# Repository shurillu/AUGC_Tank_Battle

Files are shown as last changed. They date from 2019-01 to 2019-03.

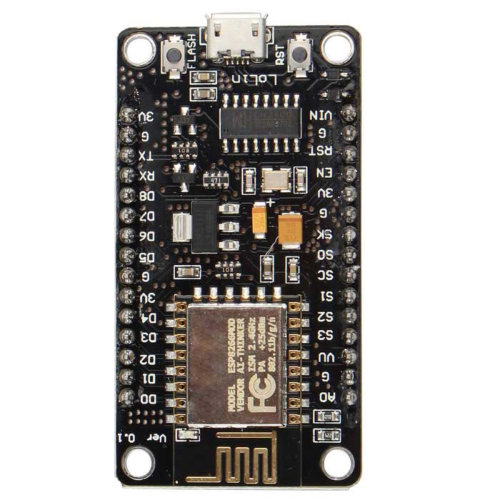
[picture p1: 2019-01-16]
images/NODEMCU_no_good.jpg

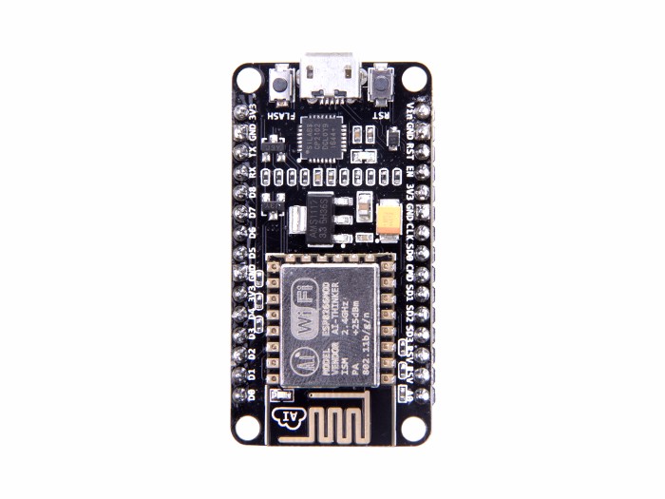
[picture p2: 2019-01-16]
images/NodeMCU_good.jpg

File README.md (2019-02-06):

# AUGC Tank Battle

This repository is for the AUGC (Arduino User Group Cagliari) Tank Battle project.
It is based on these two project:
+ **[SMARS modular robot](https://www.thingiverse.com/thing:2662828)**
+ **[Tank Go!](https://www.thingiverse.com/thing:2770957)**

Some mods are applied (for example, we use the NodeMCU 1.0 board in spite of Linkit 7697 board) in order to lower the total cost and applying little enhancements.

***Actually the project is in a alpha release: it work but not all functionalities are implemented.***

## Index

+ [To do list](#To-do-list)
+ [BOM (Bill of Materials)](#BOM-Bill-of-Materials)
+ [Printing instruction](#Printing-instruction)

## Tank functionalities
Here all the functionalities actually implemented.
+ **Wifi/Blynk connection**. If the tank cannot connect to the WiFi network or to the Blynk server (custom or official one), it will start the hotspot (SSID and password customizable) and shake the turret 3 times (NAK emote - configurable). Once connected to the hotspot, a captive portal will be displayed and it is possible to configure:
  + the WiFi credentials
  + the tank hotspot SSID and optionally the password
  + the Blynk server address (URL or IP), the Blynk server port and the Blynk token).
  
  If a connection to the Blynk server will be established, the tank shake the turret once (ACK emote - configurable)
+ **Battery management**. If the battery voltage go below a threshold (3.5V - customizable) the thank will move anymore. If the voltage raise up, the tank will move again.
+ **Ammo management**. There are several functionalities:
  + *recharging time*. Every time the tank shoot a round, it must wait a while (1500 millisecond - customizable) after shooting again. 
  + *max ammos*. The tank starts with a limited ammo quantity (20 - customizable). 
  + *current ammos*. Every time the tank shoot an ammo, the current ammos decrease. When the current ammos are zero, the tank will shoot anymore.
  + *auto regenerating ammos*. The ammos will regenerating every 7000 milliseconds (customizable). In order to regenerate ammos the tank needs to not fire. If fire a round, the regenerating timer will reset.
+ **Damage management**. There are several functionalities:
  + *max damage*. The total hit point of the tank (200 - customizable).
  + *ammo damage*. The damage of a single shoot (10 - customizable).
  + *current damage*. Every time the tank will be hit, the current damage will increased by the ammo damage. If the current damage reach the total hit points (max damage) the tank will move anymore. In order to move again, you have to repair the tank (see below)
  + *repair tank*. If the tank max out the total damage (no more hit points) the repair button will be enabled. In order to repair the tank and get moving it again, quickly press repeatedly the repair button to empty the damage bar.
+ **Moving management**. The tank can move itself and its turret using the custom Blynk app. If the voltage of the battery is below a threshold (see battery management) or if the tank is damaged (see damage management) the tank will no move.
+ **Configuration**. in the "CONFIG" tab of the custom Blynk app it is possible to configure the leftmost,  the rightmost and the center turret position.

## To do list
#### Software related
+ [ ] Multiplayer platform
+ [ ] Audio fx
+ [ ] Drive with accelerometers
+ [x] WifiManager and custom personalization
+ [x] Damage routines
+ [x] Repair routines
+ [x] Discharging and recharging ammos
+ [x] Blynk interface
+ [x] Moving the tank
+ [x] Moving the turret
+ [x] Shoot (with ID)
+ [x] Receive (and decode) shooter ID

#### Repository related
+ [ ] Tools/Hardware section
+ [ ] Arduino IDE/library configuration
+ [ ] Assembling section
+ [x] 3D printing section
+ [x] BOM Section
+ [x] Creating and populating repository

#### 3D files related
+ [ ] Upgrade the IR turret cover and the IR cover to accomodate a wireless camera for FPV playing.
+ [ ] Modify the Track_32PCS.stl file to slightly increase the center joint hole diameter and reduce the lateral joint hole diameter.
+ [x] IR_Cover.stl - Make a little socket/hetch for the IR Receiver terminals. Make some wings to keep in place the cover.

#### Harware related
+ [ ] Circuit for driving more current to the IR diode. 
+ [ ] Circuit for driving two IR diodes (dual cannon turret "Turret_X.stl").

## BOM (Bill of Materials)
Here what you need to build one:
+ **NodeMCU 1.0** - *Pay attention* that there are several models of NodeMCU: they can differ from the **USB to Serial chip** (CP2102 or CH340G) and/or from the **size**. You can identify which NodeMCU is ok by looking at the pin labels: a good ones have the pin labels printed all in the same row ([see this image](https://github.com/shurillu/AUGC_Tank_Battle/blob/master/images/NodeMCU_Comparison.jpg)). [I have this one](https://www.aliexpress.com/item/Nodo-MCU-bordo-di-Sviluppo-di-Kit-V3-CP2102-NodeMCU-Motor-Shield-Wifi-Esp8266-Esp-12e/32953905540.html)
+ **NodeMCU 1.0 Motor Shield** - It use the L293D driver and **MUST** be compatible with the NodeMCU 1.0. In the previous link you can find both (NodeMCU and motor shield).
+ **N20 6 Volt DC motor** - *You need two of them*. I use the 200 RPM version (the tank climbs obstacles with no hassle and is still speedy). Feel free to experiments with other RPMs. [Here an example](https://www.aliexpress.com/item/Spedizione-Gratuita-DC-3-v-6-v-12-v-N20-Mini-Micro-Metal-Gear-Motore-con/32953037195.html). 
+ **9g Servo Motor** - A 9g Servo motor for turret movement. You can choose between plastic or metal geared servo, it's up to you. If you buy the cheap chinese version, my advice is to buy several because sometimes they are faulty. [Here an example](https://www.aliexpress.com/item/100-NUOVO-Commercio-All-ingrosso-SG90-9g-Micro-Servo-Motore-Per-Robot-6CH-RC-Elicottero-Aereo/32831149040.html).
+ **5V 2A step up/boost converter** - There are several models, some with fixed output voltage (smaller in size), other with a voltage adjust potentiometer (bigger in size). If you choose the boost converter with the voltage adjust you can squeeze more power from the motors (setting the output voltage to 6 Volt!).  [I have this one](https://www.aliexpress.com/item/DC-DC-Auto-Boost-Buck-adjustable-step-down-Converter-XL6009-Module-Solar-Voltage/32639790122.html).
+ **TSOP38238 IR receiver** - Infrared receiver with IR filter and embedded demodulator. You can buy it [here](https://www.aliexpress.com/item/10-pz-100-nuovo-e-originale-TSOP38238-Ricevitore-IR-I-Moduli-per-I-Sistemi-di-Controllo/32947920639.html) or at your local retail seller (or wherever you want).
+ **5mm 940nm 50mA IR diode transmitter** - There are several models, I choose a model with an irradiation angle of 20 degree, in order to concentrate the irradiation power on the front of the diode. If you want to use the "Turret_X.stl" turret, you need two of this diode.
+ **100K Ohm 1/4W 1% resistor** - Used as a voltage divider, we need it to read the battery voltage.
+ **180 Ohm 1/4W 5% resistor** - Used as a current limiter for the IR diode. If you want to use the "Turret_X.stl" turret, you need two of this resistor.
+ **1S LiPo battery** - The tank main power source, 600mA 5C at least. Max dimensions are 55mm x 40mm x 9mm. [This one could be a good choice - not tested yet](https://hobbyking.com/en_us/turnigy-nano-tech-750mah-1s-70c-lipo-pack-jst-walker-hr-tech.html).
+ **Battery connectors** - A connector that match with the battery connector. *You need two of them* (one for the tank, optionally one for the battery charger). For example, if you choose the battery as above, [you need these](https://www.aliexpress.com/item/2-10-Pairs-100-150mm-2-Spille-Connettore-JST-Spina-del-Cavo-Maschio-Femmina-Per-RC/32870752993.html).
+ **LiPo charger** - (optional) A little charger for the LiPo. A good choice is a charger with the TP4056 chip. [Here a good one](https://www.aliexpress.com/item/Smart-Electronics-5V-Micro-USB-1A-18650-Lithium-Battery-Charging-Board-With-Protection-Charger-Module-for/32500042672.html).
+ **Dupont pin header connector kit** - A kit to make male/female dupont connectors (2.54 mm). [Here a good one](https://www.aliexpress.com/item/620-pz-Dupont-Connector-2-54mm-Dupont-Cavo-Ponticello-linea-di-Spille-Header-Kit-di-Alloggiamento/32950939016.html). Alternatively you can buy already crimped cables [like these](https://www.aliexpress.com/item/Dupont-line-120pcs-10cm-male-to-male-male-to-female-and-female-to-female-jumper-wire/32825558073.html). Pay attention to choose one with at least a *female connector* and *30cm long*.
+ **M3 nuts** - *You need two of them*, used in conjunction with the grub screw to bolt the main wheels. You can find it at your harware local reseller or buy a [kit like that (buy the cap/socket head kit)](https://www.aliexpress.com/item/250pc-set-A2-Stainless-Steel-M3-Cap-Button-Flat-Head-Screws-Sets-Hex-Socket-Bolt-With/32811514698.html).
+ **M3 6mm grub screw** - *You need two of them*, used in conjunction with the nuts to bolt the main wheels. You can find it at your harware local reseller or buy a [kit like that](https://www.aliexpress.com/item/50-pz-M3x6mm-Bullone-di-Fissaggio-In-Acciaio-Al-Carbonio-autofilettanti-Vite-A-Esagono-Incassato-Grub/32669329846.html).
+ **M2 8mm screw** - *You need eight of them*, better if they are the self tapping version. Used to bolt together the tank chassis. You can find it at your harware local reseller or buy a [kit like that](https://www.aliexpress.com/item/100-pz-DIN7982-M1-4-M1-7-M2-M2-3-M2-6-KA-Elettronico-Piccole-Viti/32955835312.html).
+ **Heat shrink tube** - Useful for insulate soldered terminals like IR receiver terminals, IR transmitter terminals. [A good one kit](https://www.aliexpress.com/item/328-Pz-8-Formati-Multi-Colore-Poliolefine-2-1-Halogen-Free-Tubi-Termorestringenti-Tubo-Assortimento-Manicotti/32891366605.html).
+ **DFPlayer module** - Optionally, used to implement the super cool audio effects. [I have this one](https://www.aliexpress.com/item/LEORY-DFPlayer-Mini-Lettore-MP3-Modulo-Vocale-Modulo-per-Arduino-bit-DAC-Uscita-Supporto-MP3-WAV/32849088916.html).
+ **MicroSD** - Optionally, used to store the MP3 sound fx. Any size is fine, up to 32GB.
+ **Mini Speaker 3mm ~ 29mm, 8 Ohm, 0.25W ~ 1W** - Optionally, a speaker for playing the sound fx. [something like that - not tested yet](https://www.aliexpress.com/item/2-PCS-1-w-eight-o-tablet-horn-the-original-way-N90-U9GT2-1420-panel-speaker/32782733427.html).

## Printing instruction

In this [section](https://github.com/shurillu/AUGC_Tank_Battle/tree/master/3D%20Files#3D-printing-instruction) you can find some instructions/advices for printing all the tanks parts.

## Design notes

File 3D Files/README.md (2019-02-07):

# 3D printing instruction

In the following table, you can find some instruction for a better printing result. When specified, enable the "Touching Build Plate" support type.

3D File | Description / advices | Supports
--------|-----------------------|---------
Chassis.stl <br> Chassis_No_Hole.stl | Chassis where all the electronics/motors will be installed. The "_no hole_" version is the same chassis but with no hole in the center. <br>Print only one. | YES
Chassis_Armor_L.stl | Left chassis armor.|YES
Chassis_Armor_R.stl | Right chassis armor.| YES
Turret_Base.stl | Base where will lay the turret. It will be bolted to the chassis armor left + right. | NO
Wheel_Armor_S_2PCS.stl <br> Wheel_Armor_T_2PCS.stl <br> Wheel_Armor_X_L.stl + Wheel_Armor_X_R.stl | Wheel Armor. You need 2x of this item. It will be bolted to the chassis armor left + right (one per side). <br>Print only one set, depending on your personal taste. | NO
Turret_Edelweiss.stl <br> Turret_MetalSlug.stl <br> Turret_PanzerIV.stl <br> Turret_Sherman.stl <br> Turret_TigerII.stl <br> Turret_X.stl | The tank turret. Print only one, depending on your personal taste. | YES
IR_Cover.stl <br> IR_Cover_New.stl | IR Receiver cover. It will be mounted on top of IR turret cover. The _new_ version have larger windows/loopholes and a notch to best fit with the IR receiver sensor. <br> Print only one.| NO
IR_Turret_Cover.stl <br> IR_Turret_Cover_New.stl| IR turret cover. It keeps the IR Receiver and it will mounted on top of the turret. The _new_ version best fit/mount on the turret and the IR cover. <br> Print only one. | NO
NodeMCU_Motor_Shield_battery.stl | Support for the NodeMCU motor shield and battery. | NO
Track_32PCS.stl | Tank tracks. You need 32x of this item. In Cura software, you can add multiples istances of the same 3D object by simply right-clicking over the object and choosing "Multiply Selected Model". | NO
Wheel_Master_grub_2PCS.stl | Master Wheel. You need 2x of this item. It will be bolted to the N20 motor axle. <br> **ADVICE:** modify the support angle threshold to 85 degree in order to force the support only for the horizontal non touching surfaces. In Cura, use the "Support Overhang Angle" parameter. Remember to rollback the parameter value to the initial value after printing the wheels. | YES
Wheel_Slave_2PCS.stl | Slave wheel. You need 2x of this item. It will be fitted in the chassis. | NO

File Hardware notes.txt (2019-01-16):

ESP8266 max pin current: 12mA
   https://www.esp8266.com/viewtopic.php?f=6&t=9815

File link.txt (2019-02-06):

Thingiverse:
   https://www.thingiverse.com/thing:2770957

GitHub:
   https://github.com/GeorgeChiou/Robot-Shield-V2.0

Linkit board 7697
   https://www.seeedstudio.com/LinkIt-7697-p-2818.html

Roboshield
   https://www.tindie.com/products/jasonleung8866/robot-shield-servo-control-board-for-linkit-7697/

interrupt:
   https://techtutorialsx.com/2016/12/11/esp8266-external-interrupts/

PWM
   https://stackoverflow.com/questions/42112357/how-to-implement-esp8266-5-khz-pwm
   http://esp8266.github.io/Arduino/versions/2.0.0-rc2/doc/reference.html

   https://www.analysir.com/blog/2017/01/29/updated-esp8266-nodemcu-backdoor-upwm-hack-for-ir-signals/

timer
   https://circuits4you.com/2018/01/02/esp8266-timer-ticker-example/
   https://github.com/esp8266/Arduino/issues/1844

Important
   https://www.esp8266.com/viewtopic.php?f=160&t=17549 

Machine Learning
   https://github.com/Microsoft/EdgeML

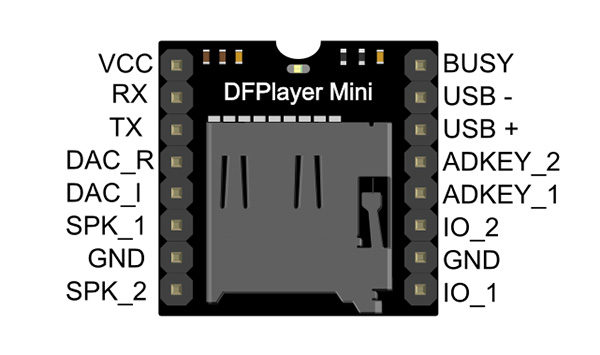
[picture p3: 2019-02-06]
datasheet/DFPlayer-pinout.jpg

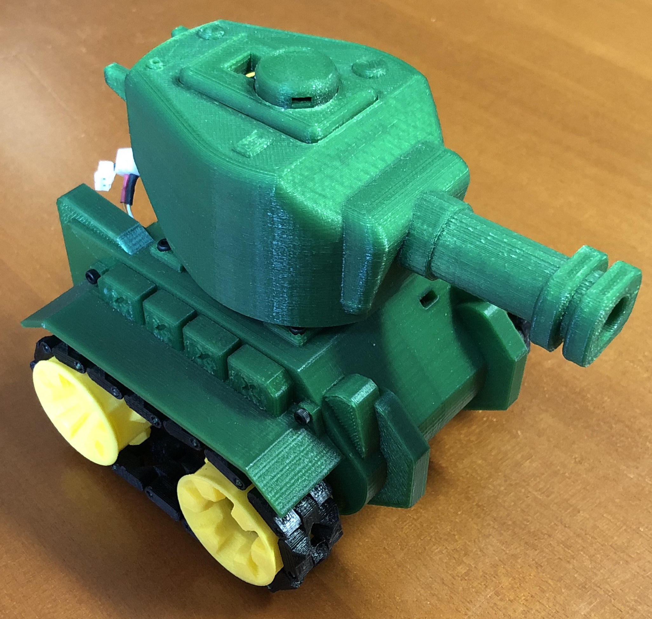
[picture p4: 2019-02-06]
images/IMG_E3739.JPG

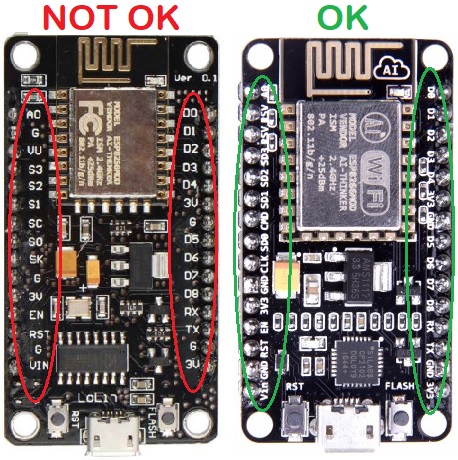
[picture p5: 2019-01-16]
images/NodeMCU_Comparison.jpg

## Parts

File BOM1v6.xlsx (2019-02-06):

Description | Portal | Price | Link | Notes
NodeMCU + Motor shield | AliExpress | 4.15 € | https://www.aliexpress.com/item/Node-MCU-Development-Kit-V3-CP2102-NodeMCU-Motor-Shield-Wifi-Esp8266-Esp-12e-diy-rc-toy/32953905540.html
NodeMCU + Motor shield | BangGood | 5.28 € | https://www.banggood.com/Wifi-Car-Dedicated-NodeMcu-Lua-ESP8266-ESP-12E-WiFi-Motor-Drive-Expansion-Board-p-1021716.html
Connettori JST x Batteria (2x) | Aliexpress | 0.55 € | https://www.aliexpress.com/item/2-10Pairs-100-150mm-2-Pin-Connector-JST-Plug-Cable-Male-Female-For-RC-BEC-Battery/32870752993.html | the (2x) mean that the link provided is for (2x) items. You just need one
Connettori JST x Batteria (5x) | BangGood | 1.43 € | https://www.banggood.com/5-Pairs-200mm-20cm-JST-Male-And-Female-Plug-Connector-Cable-ESC-Extension-Cable-p-1125803.html | the (5x) mean that the link provided is for (5x) items. You just need one
Boost converter | AliExpress | 0.48 € | https://www.aliexpress.com/item/MT3608-DC-DC-Step-Up-Converter-Booster-Power-Supply-Module-Boost-Step-up-Board-MAX-output/32964702757.html
Boost converter | BangGood | 1.16 € | https://www.banggood.com/1pcs-MT3608-2A-DC-DC-Adjustable-Step-Up-Power-Module-Booster-Power-Module-p-1213134.html
IR Receiver (TSOP38238) (5x) | AliExpress | 1.87 € | https://www.aliexpress.com/item/5pcs-lot-TSOP38238-IC-IR-RCVR-MOD-38KHZ-DOME-AXIAL-38238-P38238-OP38238/32876790151.html | the (5x) mean that the link provided is for (5x) items. You just need one
 | BangGood
N20 6V DC motor 200RPM 2x | AliExpress | 1.78 € | https://www.aliexpress.com/item/Free-Shipping-DC-3V-6V-12V-N20-Mini-Micro-Metal-Gear-Motor-with-Gearwheel-DC-Motors/32953037195.html | here you need two of them
N20 6V DC motor 200RPM 2x | BangGood | 3.51 € | https://www.banggood.com/GA12-N20-DC-6V-200RPM-Mini-Metal-Gear-Motor-With-Gearwheel-p-1214666.html | here you need two of them
LiPo battery | AliExpress | 3.00 € | https://www.aliexpress.com/item/3-7V-1200mAh-25C-Lipo-Battery-for-Syma-X5-X5C-X5SW-X5SC-X5S-X5SC-1-M18/32861614765.html
LiPo battery | BangGood | 6.16 € | https://www.banggood.com/3_7V-1200mAH-LiPo-Battery-for-Syma-X5HC-X5HW-RC-Drone-Quadcopter-p-1393763.html
Servo motor SG90 9g | AliExpress | 0.83 € | https://www.aliexpress.com/item/100-NEW-Wholesale-SG90-9G-Micro-Servo-Motor-For-Robot-6CH-RC-Helicopter-Airplane-Controls-for/32831149040.html
Servo motor SG90 9g | BangGood | 2.02 € | https://www.banggood.com/TowerPro-SG90-Mini-Gear-Micro-Servo-9g-For-RC-Airplane-Helicopter-p-1009914.html
5mm IR diode transmitter (10x) | AliExpress | 0.67 € | https://www.aliexpress.com/item/GREATZT-5mm-940nm-LEDs-Infrared-Emitter-and-IR-Receiver-Diode-10pairs-Diodes-301A/32951365819.html | the (10x) mean that the link provided is for (10x) items. You just need one
5mm IR diode transmitter (50x) | BangGood | 4.57 € | https://www.banggood.com/100pcs-5mm-940nm-IR-Infrared-Diode-Launch-Emitter-Receive-Receiver-LED-p-1205410.html | the (50x) mean that the link provided is for (50x) items. You just need one
Dupont pin header connector kit (male/female) 30cm | AliExpress | 1.03 € | https://www.aliexpress.com/item/Dupont-line-120pcs-10cm-male-to-male-male-to-female-and-female-to-female-jumper-wire/32825558073.html
Dupont pin header connector kit (male/female) 30cm | BangGood | 1.87 € | https://www.banggood.com/30cm-40pcs-Female-To-Female-Breadboard-Wires-Jumper-Cable-Dupont-Wire-p-90154.html
M3 nuts x2 (100x) | AliExpress | 6.64 € | https://www.aliexpress.com/item/250pc-set-A2-Stainless-Steel-M3-Cap-Button-Flat-Head-Screws-Sets-Hex-Socket-Bolt-With/32811514698.html | the (100x) mean that the link provided is for (100x) items. You just need two
M3 nuts x2 (100x) | BangGood | 3.14 € | https://www.banggood.com/100pcs-M3-Hexagon-Hex-Screw-Bolts-Nut-3mm-Diameter-p-1009552.html | the (100x) mean that the link provided is for (100x) items. You just need two
M3 grub x2 (50x) | AliExpress | 1.78 € | https://www.aliexpress.com/item/50pc-M3x6mm-Carbon-Steel-Bolt-Fastener-Self-tapping-Screw-Hex-Socket-Grub-Screws-Headless-Nuts-Assortment/32669329846.html | the (50x) mean that the link provided is for (50x) items. You just need two
M3 grub x2 (20x) | BangGood | 6.28 € | https://www.banggood.com/200Pcs-Stainless-Steel-Allen-Head-Socket-Hex-Set-Grub-Screw-Assortment-p-1143437.html | the (50x) mean that the link provided is for (50x) items. You just need two
M2 socketed cap 8mm x8 (100x) | AliExpress | 1.18 € | https://www.aliexpress.com/item/100Pcs-DIN7982-M1-4-M1-7-M2-M2-3-M2-6-KA-Electronic-Small-Screws-Self/32955835312.html | the (100x) mean that the link provided is for (100x) items. You just need eight
M2 8mm self tapping 8x (100x) | BangGood | 2.25 € | https://www.banggood.com/M2-6-10mm-Bronze-Self-Tapping-Phillips-Screws-Tone-Flat-Head-Round-Rivet-Wood-Screws-p-1252080.html | the (100x) mean that the link provided is for (100x) items. You just need eight
Heat shrink tube | AliExpress | 1.49 € | https://www.aliexpress.com/item/328Pcs-8-Sizes-Multi-Color-Polyolefin-2-1-Halogen-Free-Heat-Shrink-Tubing-Tube-Assortment-Sleeving/32891366605.html
Heat shrink tube | BangGood | 2.99 € | https://www.banggood.com/DANIU-Heat-Shrink-Shrinking-Tubing-Tube-Wire-Wrap-Cable-Sleeve-Kit-Set-p-1162246.html
Mini lettore MP3 (DFPlayer) | AliExpress | 0.84 € | https://www.aliexpress.com/item/LEORY-DFPlayer-Mini-MP3-Player-Module-for-Arduino-24-bit-DAC-Output-Voice-Module-Support-MP3/32849088916.html
Mini lettore MP3 (DFPlayer) | BangGood | 2.18 € | https://www.banggood.com/DFPlayer-Mini-MP3-Player-Module-For-Arduino-p-969191.html
Speaker (2x) | AliExpress | 0.45 € | https://www.aliexpress.com/item/2-PCS-1-w-eight-o-tablet-horn-the-original-way-N90-U9GT2-1420-panel-speaker/32782733427.html | the (2x) mean that the link provided is for (2x) items. You just need one
Speaker (10x) | BangGood | 3.50 € | https://www.banggood.com/10pcs-Oval-Horn-8Ohm-1W-Speaker-Tablet-PC-Speakers-Loudspeaker-Horn-30204mm-p-1111972.html | the (10x) mean that the link provided is for (10x) items. You just need one
Battery charger | AliExpress | 0.25 € | https://www.aliexpress.com/item/Smart-Electronics-5V-Micro-USB-1A-18650-Lithium-Battery-Charging-Board-With-Protection-Charger-Module-for/32500042672.html
Battery charger | BangGood | 0.87 € | https://www.banggood.com/TP4056-Micro-USB-5V-1A-Lithium-Battery-Charging-Module-Board-TE585-Lipo-Charger-p-1225993.html
100K Ohm 1/4W 1% (voltage divider)
180 Ohm 1/4W 5% (IR diode current limiter)

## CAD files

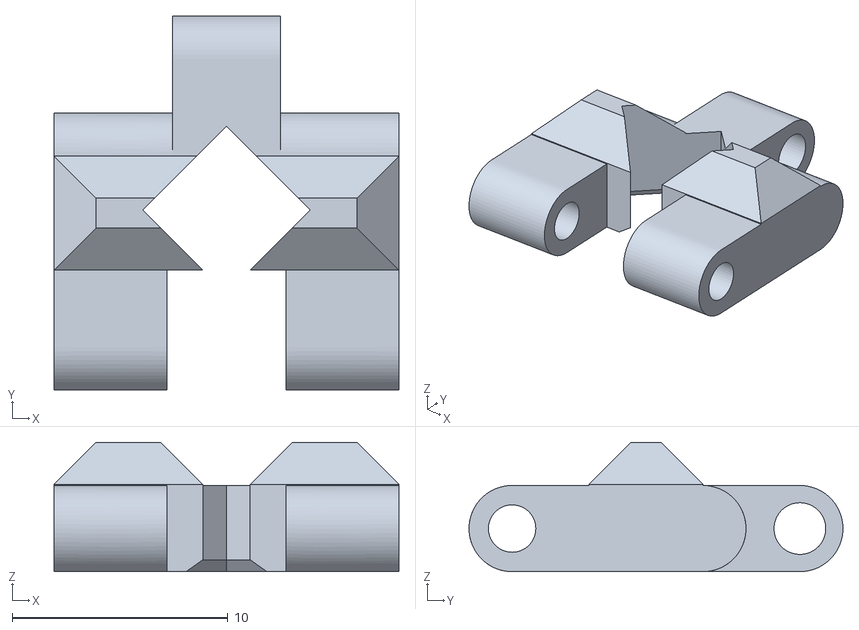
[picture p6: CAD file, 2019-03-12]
3D Files/Track_32PCS_new.stl
16.0 x 17.4 x 6.00

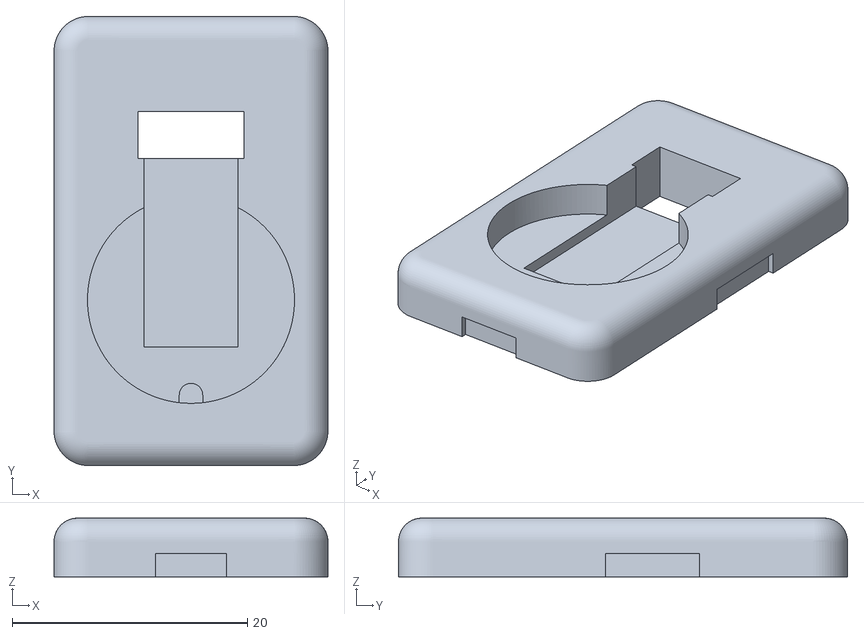
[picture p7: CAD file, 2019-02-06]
3D Files/IR_Turret_Cover_new.stl
23.3 x 38.2 x 5.00

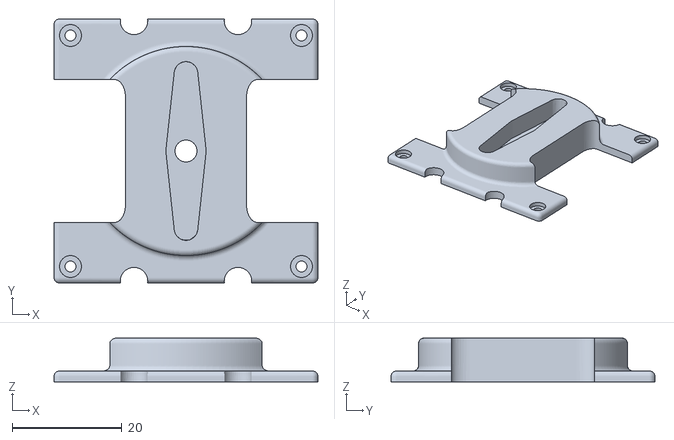
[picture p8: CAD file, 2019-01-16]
3D Files/Turret_Base.stl
48.0 x 48.0 x 8.00

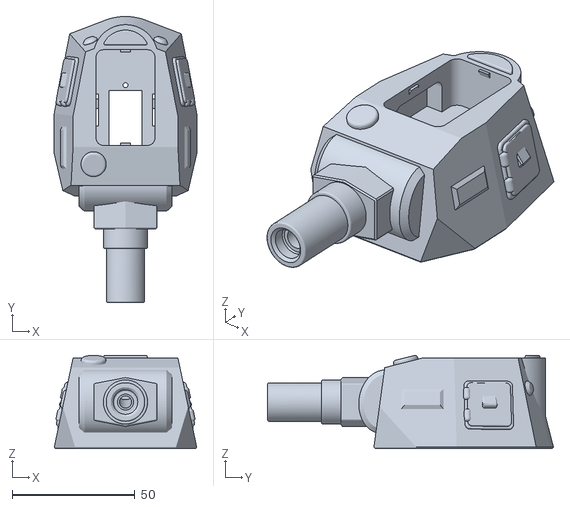
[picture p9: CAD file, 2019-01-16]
3D Files/Turret_PanzerIV.stl
58.1 x 116.6 x 38.0

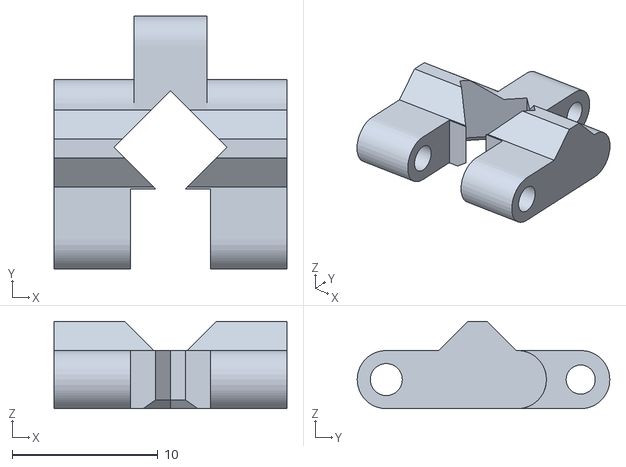
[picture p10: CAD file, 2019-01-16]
3D Files/Track_32PCS.stl
16.0 x 17.4 x 6.00

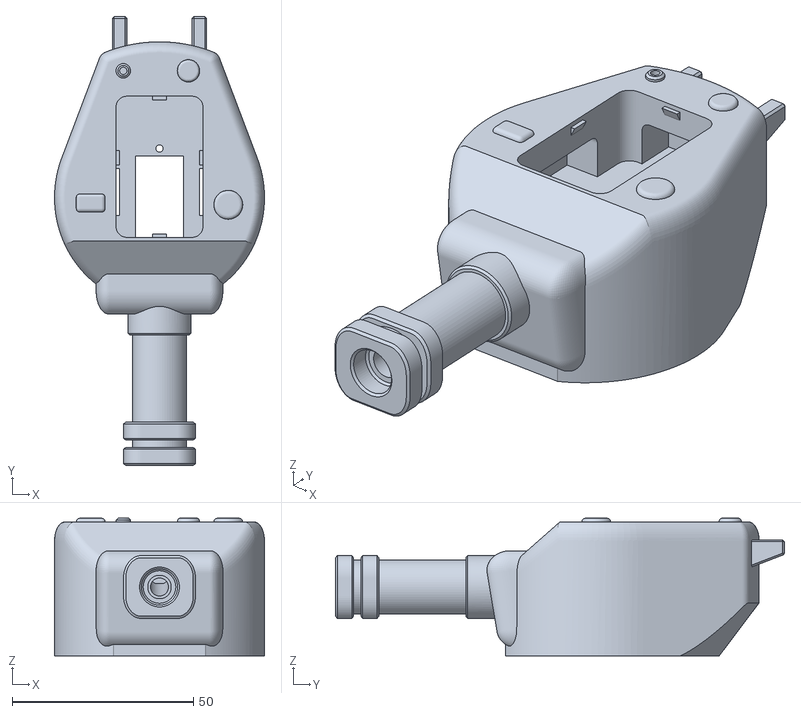
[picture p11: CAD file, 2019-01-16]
3D Files/Turret_Sherman.stl
58.0 x 124.0 x 38.0

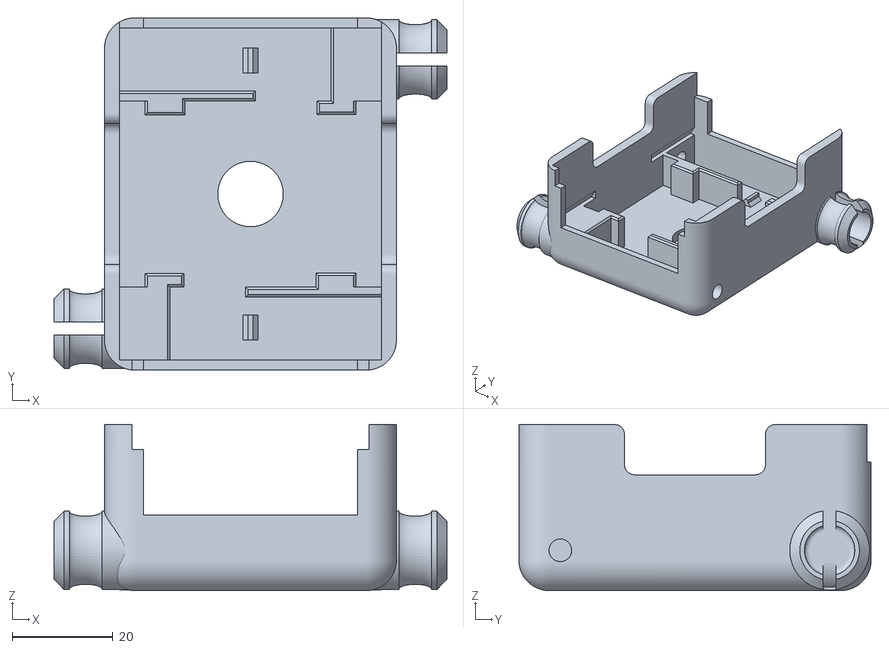
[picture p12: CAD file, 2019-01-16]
3D Files/Chassis.stl
78.1 x 70.0 x 33.0

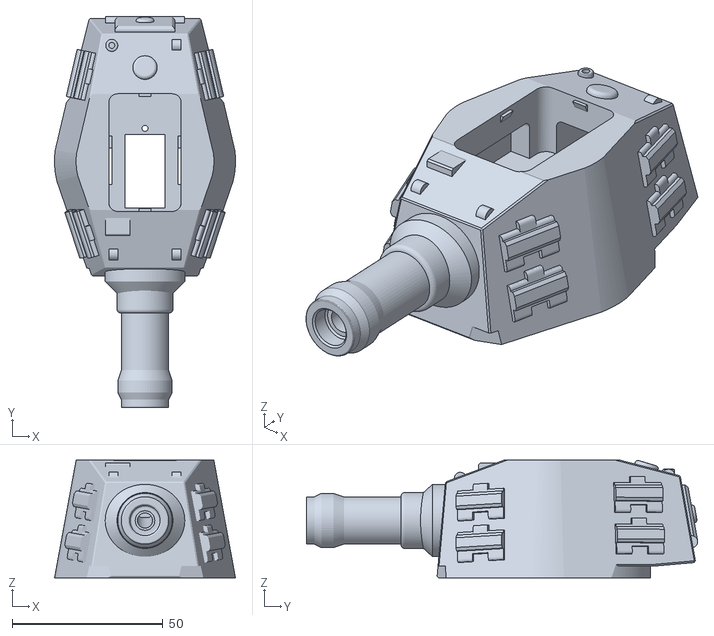
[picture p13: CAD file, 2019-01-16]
3D Files/Turret_TigerII.stl
59.9 x 129.6 x 39.0

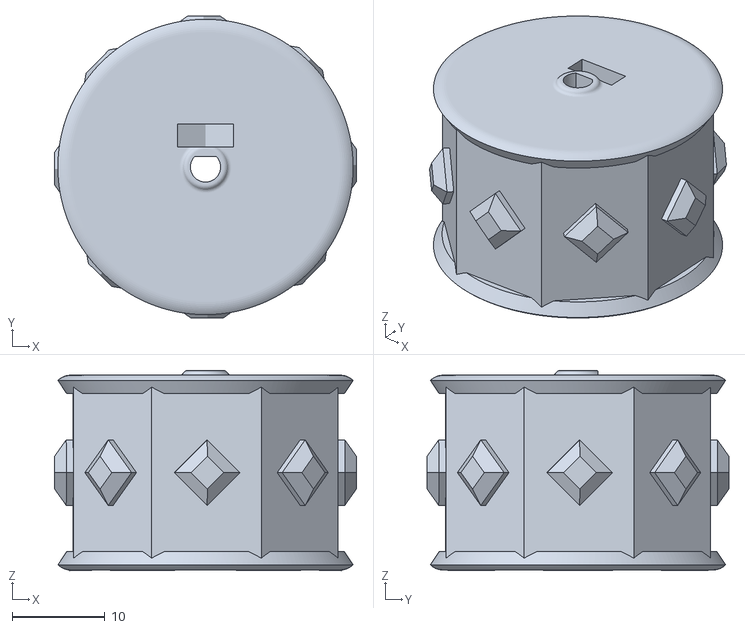
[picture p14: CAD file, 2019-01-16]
3D Files/Wheel_Master_grub_2PCS.stl
32.5 x 32.5 x 21.5

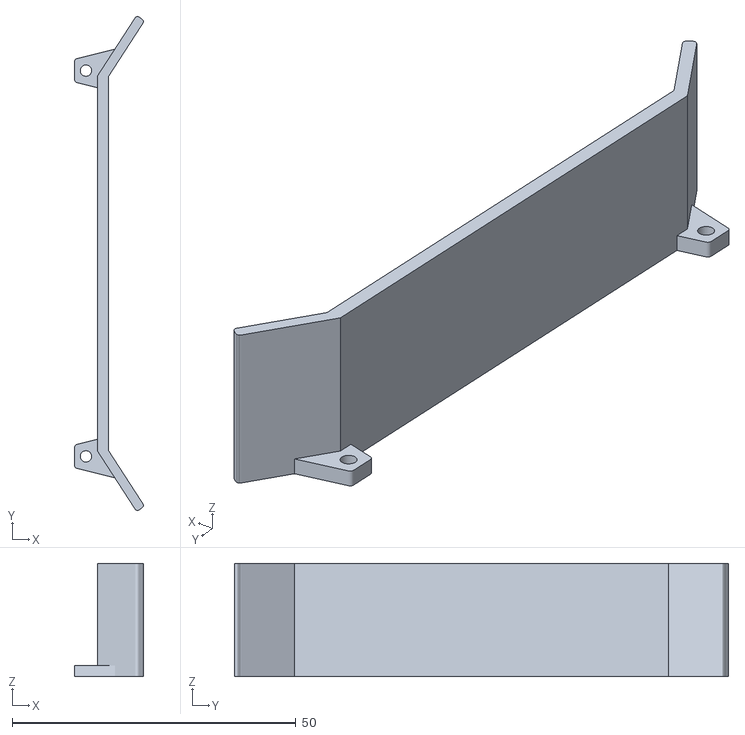
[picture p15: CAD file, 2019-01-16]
3D Files/Wheel_Armor_S_2PCS.stl
12.1 x 87.1 x 20.0

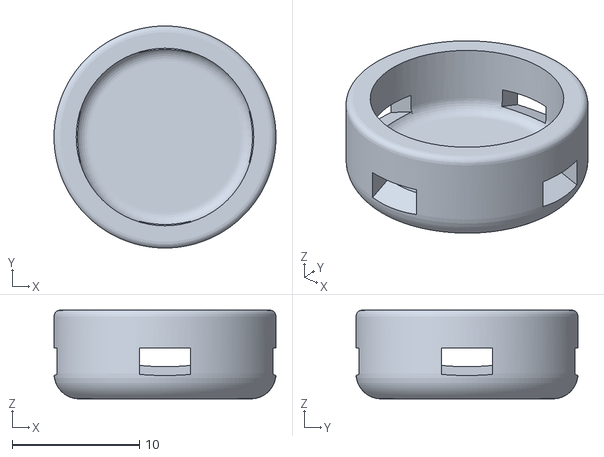
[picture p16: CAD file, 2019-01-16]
3D Files/IR_Cover.stl
17.5 x 17.5 x 7.00

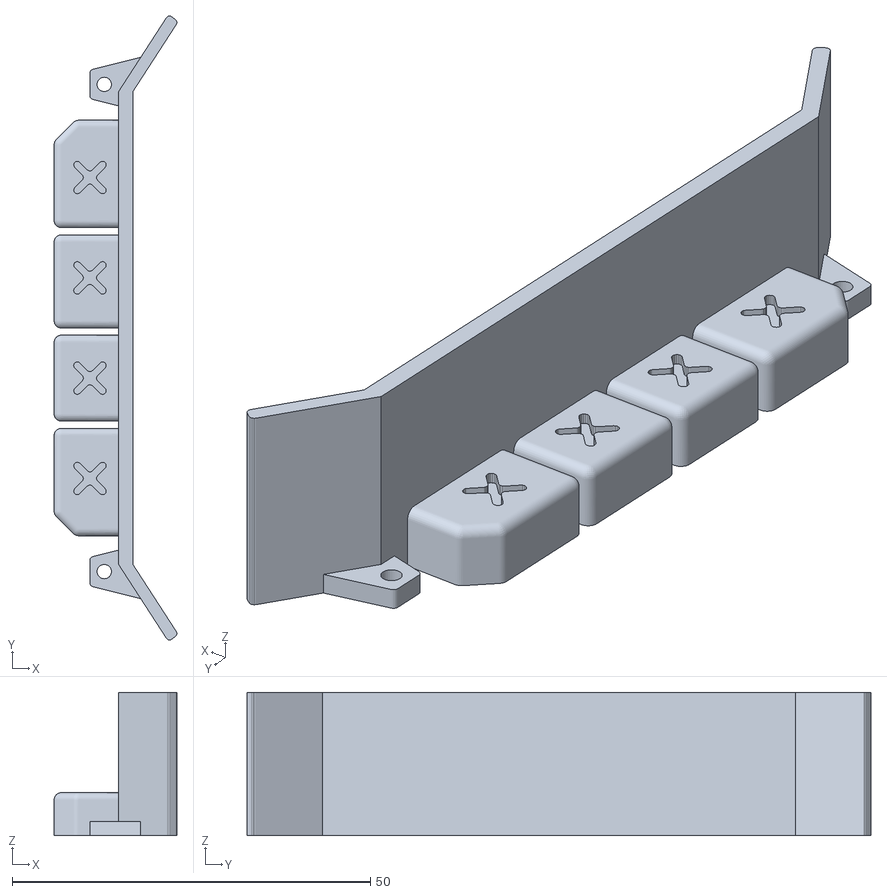
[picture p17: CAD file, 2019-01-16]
3D Files/Wheel_Armor_T_2PCS.stl
17.1 x 87.1 x 20.0

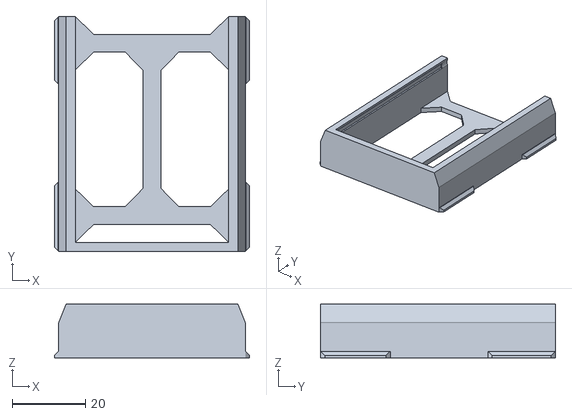
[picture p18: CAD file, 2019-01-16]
3D Files/NodeMCU_Motor_Shield_battery.stl
53.2 x 64.0 x 14.7

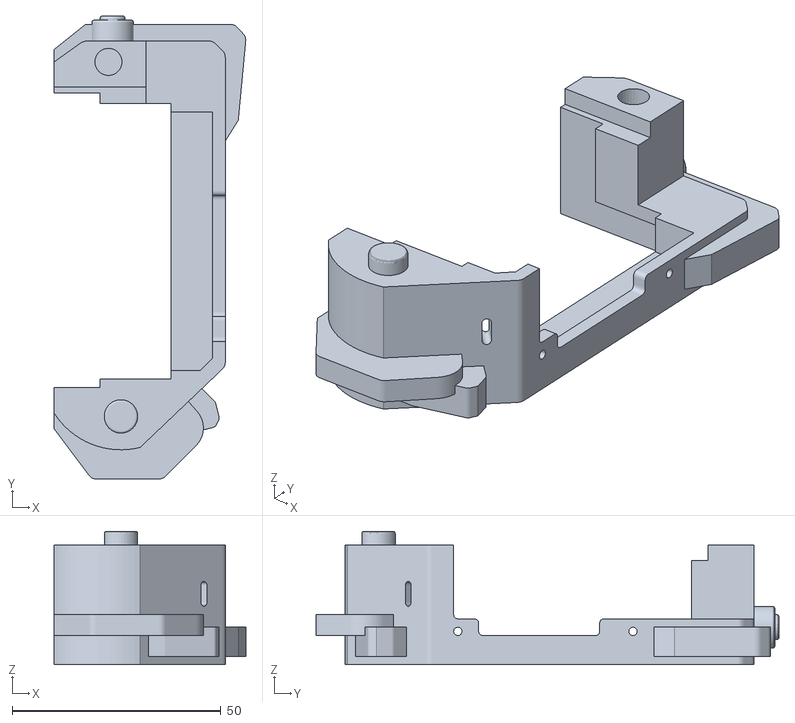
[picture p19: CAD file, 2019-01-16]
3D Files/Chassis_Armor_L.stl
45.9 x 111.0 x 32.0

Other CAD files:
3D Files/Wheel_Slave_2PCS.stl
3D Files/Turret_X.stl
3D Files/IR_Turret_Cover.stl
3D Files/Chassis_Armor_R.stl
3D Files/Turret_Edelweiss.stl
3D Files/Turret_MetalSlug.stl
3D Files/Wheel_Armor_X_L.stl
3D Files/Wheel_Armor_X_R.stl

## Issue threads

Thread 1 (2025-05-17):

Is this still active?

SteveGoral, 2025-05-17:
I appear to have found this rather late, is this still being developed?  Or has it bee superceded by anything else?  It looks and sounds amazing.

shurillu, 2025-05-17:
Hello Steve,
   the main issue is Blynk: when I developed the project, the Blynk platform was free and you had the opportunity to build your own server.
Now is a paid platform.
I still have some tanks, a custom server on a Raspberry Pi Zero W, the old Blynk phone app and I use it in some events (like local Arduino Days).
If you wanna try, I can give you an hand with the server, but for the client (the phone app) you have to find the old Blynk app (maybe for Android should be easier than iOS platform that needs to be jailbroken).
I have in my mind the idea to migrate it to an ESP32 platform and a web based application (websockets), but time is a bad beast and now I'm in love with Meshtastic project ;-)

SteveGoral, 2025-05-17:
I know exactly what you mean about time being a bad beast, thanks for the reply, I'd love to take you up on your offer but it's probably a bit out of my league.  Best of luck with any future projects.

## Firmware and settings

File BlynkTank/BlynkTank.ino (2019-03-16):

#define BLYNK_PRINT   Serial          // must be before #include <BlynkSimpleEsp8266.h>

#include <ESP8266WiFi.h>
#include <BlynkSimpleEsp8266.h>
#include "CTank.h"

// default colors
#define BLYNK_GREEN     "#23C48E"
#define BLYNK_BLUE      "#04C0F8"
#define BLYNK_YELLOW    "#ED9D00"
#define BLYNK_RED       "#D3435C"
#define BLYNK_DARK_BLUE "#5F7CD8"
#define BLYNK_GRAY      "#606060"


// Blynk server connection timeout
#define BLYNK_TIMEOUT           5000 // milliseconds

// When the tank is powered, it shot a codes and try to read it. If it happen, 
// the hotsopt is forced to load. Useful if you need to enter in hotspot mode.
// To do it, place the turret cannon in front of a wall (the hand works just fine)
#define HOTSPOT_REQUEST_TIMEOUT 3000 // milliseconds

#define VIRTUAL_VOLTAGE  V0           // voltage virtual pin. This value is written by the tank to the app
                                      //    Range: [0..4200]

#define VIRTUAL_JOYSTICK V1           // joystick virtual pin. This value is written by the app to the tank 
                                      // It's a combined value:
                                      //    param[0] -> x value. Range: [-1023..+1023] 
                                      //    param[1] -> y value. Range: [-1023..+1023]

#define VIRTUAL_TURRET   V2           // Turret virtual pin. This value is written by the app (turret movement)
                                      // and by the tank (initial setup)
                                      //    Range: auto (calculated by the tank settings)

#define VIRTUAL_FIRE_BTN V3           // fire push button virtual pin. This value is written by the app to the tank
                                      //    Range: 0 (not pressed), 1 (pressed)

#define VIRTUAL_REPAIR_BTN V4         // repair push button virtual pin. This value is written by the app to the tank
									  //    Range: 0 (not pressed), 1 (pressed)

#define VIRTUAL_TERMINAL V5           // terminal virtual pin. This value is written by the tank to the app
                                      // used as log terminal

#define VIRTUAL_ACCELEROMETER V6      // accelerometer virtual pin [FUTURE ADD ONS]

#define VIRTUAL_HITPOINT V7           // hit points virtual pin. This value is written by the tank to the app
									  //    Range: auto (calculated by the tank settings)

#define VIRTUAL_AMMO V8               // ammos virtual pin. This value is written by the tank to the app
									  //    Range: auto (calculated by the tank settings)

// virtual pins for settings page
#define VIRTUAL_TURRET_CENTER V10    // central server position
#define VIRTUAL_TURRET_LEFT   V11    // left server position
#define VIRTUAL_TURRET_RIGHT  V12    // right server position
#define VIRTUAL_SAVE_SLIDER   V13    // save method


// Battery voltage threshold. If the battery voltage is below this threshold, all the functionalities are disabled
// (motors, shoot, etc).
#define BATTERY_VOLTAGE_THRESHOLD 3500  // mA


// global varibles ----------------------------------------------------------------------------------------------------
WidgetTerminal terminal(VIRTUAL_TERMINAL); // for the terminal log
BlynkTimer voltageTimer;
Ticker needRepairTimer;
bool couldMove;
bool couldRepair;

CTank myTank;
uint8_t ammos;

bool turretRepairMovement;

uint8_t defaultVolume;
uint16_t fxID_Shoot;


uint16_t fxID_Error;
uint16_t fxID_Start;
uint16_t fxID_Damage;
uint16_t fxID_Burn;

// timer handlers -----------------------------------------------------------------------------------------------------
void voltageTimerEvent(void){
	uint16_t voltage = myTank.getBatteryVoltage();
	Blynk.virtualWrite(VIRTUAL_VOLTAGE, voltage);
	if (voltage < BATTERY_VOLTAGE_THRESHOLD) {
		couldMove = false;
		Blynk.setProperty(VIRTUAL_VOLTAGE, "color", BLYNK_RED);
		terminal.printf("[%07lu] LOW BATTERY %umV!!!\n", millis() / 100, voltage);
		terminal.flush();
	}
	else {
		couldMove = true;
		Blynk.setProperty(VIRTUAL_VOLTAGE, "color", BLYNK_GREEN);
	}
}

void needRepairTimerEvent(void) {
	if (turretRepairMovement)
		myTank.moveTurretDegree(60);
	else
		myTank.moveTurretDegree(120);
	turretRepairMovement = !turretRepairMovement;

}

void updateTurretSlider(void) {
	Blynk.setProperty(VIRTUAL_TURRET, "min", myTank.getServoMin_us());
	Blynk.setProperty(VIRTUAL_TURRET, "max", myTank.getServoMax_us());
	Blynk.virtualWrite(VIRTUAL_TURRET, (myTank.getServoMin_us() + myTank.getServoMax_us())/2);
}

void soundFXInit(void) {
	defaultVolume = 0x20;
	fxID_Error    = 0x01;
	fxID_Start    = 0x02;
	fxID_Burn     = 0x03;
	fxID_Shoot    = 0x04;
	fxID_Damage   = 0x05;

}

void blynkTankInit(void) {
	Blynk.virtualWrite(VIRTUAL_TURRET_CENTER, 1500 - myTank.getServoCenter());
	Blynk.virtualWrite(VIRTUAL_TURRET_LEFT, 2000 - myTank.getServoMax_us());
	Blynk.virtualWrite(VIRTUAL_TURRET_RIGHT, 1000 - myTank.getServoMin_us());
	Blynk.setProperty(VIRTUAL_SAVE_SLIDER, "color", BLYNK_GREEN);

	Blynk.setProperty(VIRTUAL_HITPOINT, "min", 0);
	Blynk.setProperty(VIRTUAL_HITPOINT, "max", myTank.getMaxHitpoint());
	Blynk.virtualWrite(VIRTUAL_HITPOINT, 0);

	ammos = myTank.getAmmo();
	Blynk.virtualWrite(VIRTUAL_AMMO, ammos);

	Blynk.setProperty(VIRTUAL_VOLTAGE, "color", BLYNK_GREEN);

	Blynk.setProperty(VIRTUAL_REPAIR_BTN, "offBackColor", BLYNK_GRAY);

	updateTurretSlider();

	// log terminal initialization
	terminal.clear();
	terminal.printf("Tank ready!\n");
	terminal.flush();

	voltageTimer.setInterval(100, voltageTimerEvent);

	myTank.shakeTurretAnimation(1);
	couldMove = true;
	couldRepair = false;
	myTank.canRespawnAmmo(true);
	myTank.setVolume(defaultVolume);

}

// callback that manage the software trimmer to center the turret
BLYNK_WRITE(VIRTUAL_TURRET_CENTER) {
	int value = param.asInt(); 
	myTank.moveTurret_us(1500 - value, true);
	myTank.setServoCenter(1500 - value);
	Blynk.setProperty(VIRTUAL_SAVE_SLIDER, "color", BLYNK_RED);
}

// callback that manage the software trimmer to set the leftmost turret position
BLYNK_WRITE(VIRTUAL_TURRET_LEFT) {
	int value = param.asInt();
	myTank.moveTurret_us(2000 - value, true);
	myTank.setServoMax_us(2000 - value);
	Blynk.setProperty(VIRTUAL_SAVE_SLIDER, "color", BLYNK_RED);
}

//callback that manage the software trimmer to set the rightmost turret position
BLYNK_WRITE(VIRTUAL_TURRET_RIGHT) {
	int value = param.asInt();
	myTank.moveTurret_us(1000 - value, true);
	myTank.setServoMin_us(1000 - value);
	Blynk.setProperty(VIRTUAL_SAVE_SLIDER, "color", BLYNK_RED);
}

// callback that manage the gesture to save the settings
BLYNK_WRITE(VIRTUAL_SAVE_SLIDER) {
	int value = param.asInt();
	if (value == 1023) {
		Blynk.virtualWrite(VIRTUAL_SAVE_SLIDER, 0);
		if (myTank.writeTankConfigFile()) {
			Blynk.setProperty(VIRTUAL_SAVE_SLIDER, "color", BLYNK_GREEN);
			updateTurretSlider();
			myTank.shakeTurretAnimation(1);
		}
		else
			myTank.shakeTurretAnimation(3);
	}
}


// Moving, joystick callback. Called every time the joystick values change
BLYNK_WRITE(VIRTUAL_JOYSTICK) {
	// move only if the battery is not depleted
	if (!couldMove)
		return;

	// move only if the tank don't need to be repaired
	if (couldRepair)
		return;

	// read the joystick position
	int joyX = param[0].asInt();
	int joyY = param[1].asInt();
	myTank.moveTank(joyX, joyY);
}

//turret callback. Called every time the turret values (position) change
BLYNK_WRITE(VIRTUAL_TURRET) {
	// move only if the battery is not depleted
	if (!couldMove)
		return;

	// move only if the tank don't need to be repaired
	if (couldRepair)
		return;

	// read the turret slider position
	int value = param.asInt();
	myTank.moveTurret_us(value); // move the turret
}

//fire button callback. Called every time the fire button is pressed
BLYNK_WRITE(VIRTUAL_FIRE_BTN) {
	// fire only if the battery is not depleted
	if (!couldMove)
		return;

	// fire only if the tank don't need to be repaired
	if (couldRepair)
		return;

	// read the fire button value
	int value = param.asInt();

	// if the button is pressed (value == 1)
	if (value == 1) {
		if (myTank.shoot()) {// shoot an ammo
			Blynk.virtualWrite(VIRTUAL_AMMO, myTank.getAmmo());
			myTank.playSound(fxID_Shoot);
			myTank.shootAnimation();
		}
	}
}

//repair button callback. Called every time the repair button is pressed
BLYNK_WRITE(VIRTUAL_REPAIR_BTN) {
	// repair only if the repair option is enabled/possible
	if (!couldRepair)
		return;

	int value = param.asInt();
	if (1 == value) {
		int currentDamage = myTank.getMaxHitpoint() - myTank.repairTank();
		Blynk.virtualWrite(VIRTUAL_HITPOINT, currentDamage);
		if (0 == currentDamage) {
			Blynk.setProperty(VIRTUAL_REPAIR_BTN, "offBackColor", BLYNK_GRAY);
			couldRepair = 0;
			needRepairTimer.detach();
			Blynk.virtualWrite(VIRTUAL_TURRET, (myTank.getServoMin_us() + myTank.getServoMax_us()) / 2);
//			myTank.moveTurret_us((myTank.getServoMin_us() + myTank.getServoMax_us()) / 2);
			myTank.moveTurret_us(myTank.getServoCenter(), true);
			myTank.canRespawnAmmo(true);
			myTank.playSound(fxID_Start);
		}
	}
}

// various system callbacks (not really useful atm)
BLYNK_CONNECTED() {
	Serial.printf("Connected to server!\n");
}
BLYNK_APP_CONNECTED() {
	Serial.printf("APP Connected\n");
}
BLYNK_APP_DISCONNECTED() {
	Serial.printf("APP Disconnected\n");
}
BLYNK_DISCONNECTED() {
	Serial.printf("Disconnected from server\n");
}

void setup()
{
	// Debug console
	Serial.begin(115200);
	delay(2000);

	soundFXInit();
	// check if the user force to start the hotsopt by placing the turret in front of a wall
	if (myTank.checkProximity(HOTSPOT_REQUEST_TIMEOUT)) {
		Serial.printf("\nProximity detected. Launching hotspot\n");
		myTank.playSound(fxID_Error);
		myTank.startHotspot();
	}


	myTank.wifiConnect();

	while (!Blynk.connected()) {
		char server[40];
		char token[40];
		strcpy(server, myTank.getBlynkServer().c_str());
		strcpy(token, myTank.getBlynkToken().c_str());
		if (myTank.isBlynkKnownByIP()) {
			Serial.printf("Connecting using IP: %s\n", myTank.getBlynkIP().toString().c_str());
			Blynk.config(token, myTank.getBlynkIP(), myTank.getBlynkPort());
		}
		else {
			Serial.printf("Connecting using server: %s\n", myTank.getBlynkServer().c_str());
			Blynk.config(token, server, myTank.getBlynkPort());
		}
		Blynk.connect(BLYNK_TIMEOUT);
		if (!Blynk.connected()) {
			Serial.printf("Unable to connect to %s server. Launching hotspot...\n", myTank.getBlynkServer().c_str());
			myTank.playSound(fxID_Error);
			myTank.startHotspot();
		}
	}

	myTank.playSound(fxID_Start);
	blynkTankInit();

}

void loop()
{
	Blynk.run(); // Blynk server synchronization
	voltageTimer.run();

//	myTank.printMP3Debug();

	// for auto regenerating ammos
	if (ammos != myTank.getAmmo()) {
		ammos = myTank.getAmmo();
		Blynk.virtualWrite(VIRTUAL_AMMO, ammos);
	}

	// if I have received an IR valid packet...
	int hitCode = myTank.getHitCode();
	if (hitCode != -1) {
		if (!couldRepair) {  // prevent get hit when repairing...
			int currentDamage = myTank.getMaxHitpoint() - myTank.gotHit();
			Blynk.virtualWrite(VIRTUAL_HITPOINT, currentDamage);
			// print it in the terminal log (with a timing reference) and flush the data
			terminal.printf("[%07lu] HIT by %02Xh\n", millis() / 100, hitCode);
			terminal.flush();
			if (myTank.getMaxHitpoint() == currentDamage) {
				myTank.moveTank(0, 0);
				myTank.playSound(fxID_Burn, true);
				Blynk.setProperty(VIRTUAL_REPAIR_BTN, "offBackColor", BLYNK_GREEN);
				needRepairTimer.attach_ms(300, needRepairTimerEvent);
				couldRepair = true;
				myTank.canRespawnAmmo(false);
			}
			else
				myTank.playSound(fxID_Damage);

		}
	}
}



/*
// hamming 4-3
// https://www.thecrazyprogrammer.com/2017/03/hamming-code-c.html
void main() {
	int data[10];
	int dataatrec[10], c, c1, c2, c3, i;

	printf("Enter 4 bits of data one by one\n");
	scanf("%d", &data[0]);
	scanf("%d", &data[1]);
	scanf("%d", &data[2]);
	scanf("%d", &data[4]);

	//Calculation of even parity
	data[6] = data[0] ^ data[2] ^ data[4];
	data[5] = data[0] ^ data[1] ^ data[4];
	data[3] = data[0] ^ data[1] ^ data[2];

	printf("\nEncoded data is\n");
	for (i = 0; i < 7; i++)
		printf("%d", data[i]);

	printf("\n\nEnter received data bits one by one\n");
	for (i = 0; i < 7; i++)
		scanf("%d", &dataatrec[i]);

	c1 = dataatrec[6] ^ dataatrec[4] ^ dataatrec[2] ^ dataatrec[0];
	c2 = dataatrec[5] ^ dataatrec[4] ^ dataatrec[1] ^ dataatrec[0];
	c3 = dataatrec[3] ^ dataatrec[2] ^ dataatrec[1] ^ dataatrec[0];
	c = c3 * 4 + c2 * 2 + c1;

	if (c == 0) {
		printf("\nNo error while transmission of data\n");
	}
	else {
		printf("\nError on position %d", c);

		printf("\nData sent : ");
		for (i = 0; i < 7; i++)
			printf("%d", data[i]);

		printf("\nData received : ");
		for (i = 0; i < 7; i++)
			printf("%d", dataatrec[i]);

		printf("\nCorrect message is\n");

		//if errorneous bit is 0 we complement it else vice versa
		if (dataatrec[7 - c] == 0)
			dataatrec[7 - c] = 1;
		else
			dataatrec[7 - c] = 0;

		for (i = 0; i < 7; i++) {
			printf("%d", dataatrec[i]);
		}
	}
}
*/

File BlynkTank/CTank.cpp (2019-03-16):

#include "CTank.h"
#include "FS.h"

ADC_MODE(ADC_TOUT) // NodeMCU ADC initialization: external pin reading values enabled

// motors pin. These values can't be modified (NodeMCU motor shield)
#define L_MOTOR_PWM_PIN D1
#define R_MOTOR_PWM_PIN D2
#define L_MOTOR_DIR_PIN D3
#define R_MOTOR_DIR_PIN D4

#define IR_TX_PIN       D5 // IR tx pin
#define IR_RX_PIN       D6 // IR rx pin
//#define TURRET_PIN      D8 // servo turret pin
#define TURRET_PIN      D0 // servo turret pin

#define MP3_TX_PIN      D8 // MP3 tx pin
#define MP3_RX_PIN      D7 // MP3 rx pin

#define TURRET_CENTER 98              // the turret center position (degree)
#define PWM_DEADBAND  300             // PWM motor threshold (below this value the motor is stopped)
#define ADC_BATTERY_COEFFICENT 1000.0 // ADC correction factor... depending on the voltage divider
#define BATTERY_VOLTAGE (4.2 / 1024.0) * ADC_BATTERY_COEFFICENT // mv
//#define MY_ID 0x53                    // one byte tank ID (this code is transmitted when the fire button is pressed)
#define MY_ID 0x0F                    // one byte tank ID (this code is transmitted when the fire button is pressed)
                                      // only first 4 bit -> 16 different codes max

// the code sent to check the proximity (if the turret is near a wall)
// used to load the hotspot
#define HOTSPOT_REQUEST_CODE    0x0A


// network defaults
#define DEFAULT_SSID         "mySSID"
#define DEFAULT_PSWD         "myPassword"
#define DEFAULT_HOTSPOT_SSID "AUGCMyTank"
#define DEFAULT_HOTSPOT_PSWD ""
#define DEFAULT_BLYNK_SERVER "blynk-cloud.com"
#define DEFAULT_BLYNK_PORT   "8080"
#define DEFAULT_BLYNK_TOKEN  "myBlynkToken"

// servo defaults
#define DEFAULT_SERVO_CENTER 1500
#define DEFAULT_SERVO_MIN_US 1000
#define DEFAULT_SERVO_MAX_US 2000

#define SERVO_RANGE 500

// how much time the tank must sense the IR carrier for starting the hotspot
#define HOTSPOT_TIMEOUT	   2000  // milliseconds

// how many seconds should try to connect to the wifi network
#define WIFI_TIMEOUT       10    // seconds

#define DEFAULT_MAX_HITPOINT       200
#define DEFAULT_AMMO_RECHARGE_TIME 1500 // milliseconds
#define DEFAULT_AMMO_DAMAGE        40
#define DEFAULT_MAX_AMMO           20
#define DEFAULT_REPAIR_VALUE       5
#define DEFAULT_AMMO_SPAWN_TIME    7000  // milliseconds


#define NETWORK_CONFIG_FILE "/network.cfg"
#define TANK_CONFIG_FILE    "/tank.cfg"

// tags for network configuration file
#define VERSION_TAG      "Version = "
#define WIFI_SSID_TAG    "WiFiSSID = "
#define WIFI_PSWD_TAG    "WiFiPassword = "
#define HS_SSID_TAG      "HotspotSSID = "
#define HS_PSWD_TAG      "HotspotPassword = "
#define BLYNK_SERVER_TAG "BlynkServer = "
#define BLYNK_PORT_TAG   "BlynkPort = "
#define BLYNK_TOKEN_TAG  "BlynkToken = "

// tags fot tank configuration file
#define SERVO_CENTER_TAG "ServoCenter = "
#define SERVO_MIN_US_TAG "ServoMin_us = "
#define SERVO_MAX_US_TAG "ServoMax_us = "



// WifiManager callbacks and variables ------------------------------------------------------------------------
bool shouldSaveConfig;

// enter in config mode
void configModeCallback(WiFiManager *myWiFiManager) {
	Serial.println("Entered config mode");
	Serial.println(WiFi.softAPIP());
	Serial.println(myWiFiManager->getConfigPortalSSID());
}

//callback notifying us of the need to save config. Only when the connection is established
void saveConfigCallback() {
	Serial.println("Should save config");
	shouldSaveConfig = true;
}
// ------------------------------------------------------------------------------------------------------------

// ammoReloadTimer callback. Used to simulate the ammo reload time 
void ammoReload(CTank* tank) {
	tank->ammoReloadDone();
//	Serial.println("Recharged");
}

// Spawn ammo callback. Used to spawn ammos when the tank is not firing
void spawnAmmo(CTank* tank) {
	tank->newAmmos(1);
}


// Humming coding... very work in progress maybe Reed Solomon codes is better
uint8_t hamming7_4Encode(uint8_t data) {
	uint8_t dataEncoded;

	// only 4 bit data;
	data = data & 0x0F;

	uint8_t p1 = ((data >> 3) & 0x01) ^ ((data >> 2) & 0x01) ^ ((data >> 1) & 0x01);
	uint8_t p2 = ((data >> 2) & 0x01) ^ ((data >> 1) & 0x01) ^ ((data >> 0) & 0x01);
	uint8_t p3 = ((data >> 3) & 0x01) ^ ((data >> 2) & 0x01) ^ ((data >> 0) & 0x01);

	dataEncoded = p3 + (p2 << 1) + (p1 << 2) + data << 3;
	
	return(dataEncoded);
}

uint8_t hamming7_4Decode(uint8_t data) {
	
	uint8_t s1 = ((data >> 6) & 0x01) ^ ((data >> 5) & 0x01) ^ ((data >> 4) & 0x01) ^ ((data >> 2) & 0x01);
	uint8_t s2 = ((data >> 5) & 0x01) ^ ((data >> 4) & 0x01) ^ ((data >> 3) & 0x01) ^ ((data >> 1) & 0x01);
	uint8_t s3 = ((data >> 6) & 0x01) ^ ((data >> 5) & 0x01) ^ ((data >> 3) & 0x01) ^ ((data >> 0) & 0x01);

	uint8_t s = (s1 << 2) + (s2 << 1) + s3;
	if (0 != s) {
		uint8_t mask = 1 << (s - 1);
		if ((data & mask) != 0)
			data = data & (!mask);
		else
			data = data | mask;
	}
	return(data >> 3);



}










CTank::CTank():CTank(false)
{
}

CTank::CTank(bool formatFS)
{
	// IR transceiver object
	m_pIRcom  = new CIR(IR_RX_PIN, IR_TX_PIN);
	m_pMP3com = new SoftwareSerial(MP3_RX_PIN, MP3_TX_PIN);
	m_pMP3com->begin(9600);

	// servo turret initialization
	m_turret.attach(TURRET_PIN);

	// motor pin initialization
	pinMode(L_MOTOR_PWM_PIN, OUTPUT);
	pinMode(R_MOTOR_PWM_PIN, OUTPUT);
	pinMode(L_MOTOR_DIR_PIN, OUTPUT);
	pinMode(R_MOTOR_DIR_PIN, OUTPUT);

	// ADC initialization (for battery voltage reading)
	pinMode(A0, INPUT);

	initFS(formatFS);
	if (!readNetworkConfigFile())
		setNetworkConfigDefaults();

	if (!readTankConfigFile())
		setTankConfigDefaults();

	m_maxHitPoints     = DEFAULT_MAX_HITPOINT;
	m_hitPoints        = DEFAULT_MAX_HITPOINT;
	m_maxAmmo          = DEFAULT_MAX_AMMO;
	m_ammo             = DEFAULT_MAX_AMMO;
	m_ammoDamage       = DEFAULT_AMMO_DAMAGE;
	m_ammoRechargeTime = DEFAULT_AMMO_RECHARGE_TIME;
	m_repairValue      = DEFAULT_REPAIR_VALUE;
	m_isReloading      = false;
	m_ammoSpawnTime    = DEFAULT_AMMO_SPAWN_TIME;
	m_canRespawnAmmo   = true;
}

CTank::~CTank()
{
	delete m_pIRcom;
	delete m_pMP3com;
}
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

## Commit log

2019-01-16 3D printing md file
    [NodeMCU_Motor_Shield_battery.stl]
2019-02-06 Preliminary V2.0.0 upload
    [BOM1v6.xlsx, IR_Turret_Cover_new.stl]
2019-03-01 AUGC Chassis
